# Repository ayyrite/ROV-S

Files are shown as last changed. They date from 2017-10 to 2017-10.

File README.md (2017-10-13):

# SIPI ROV-S
Documents concerning the SIPI ROV-S including electrical diagrams, stl files, and an assembly manual.

### ROV-S ROS code
ROS code for ROV-S project can be found by clicking this link -> [ROV-S Code](https://github.com/jmwest0774/rovs)

### To begin manual control of the ROV-S
* Turn on the ROV-S Intel NUC and Arduino motorshields.
* Attach a gamepad to one of the open USB ports located on the Intel NUC or USB hub connected to the Intel NUC.
* Open up a new terminal in Ubuntu.
* Type the following command below in the Ubuntu terminal that was just opened:
>
`roslaunch rovs rovs.launch`

* The ROV-S can now be controlled with the connected gamepad.

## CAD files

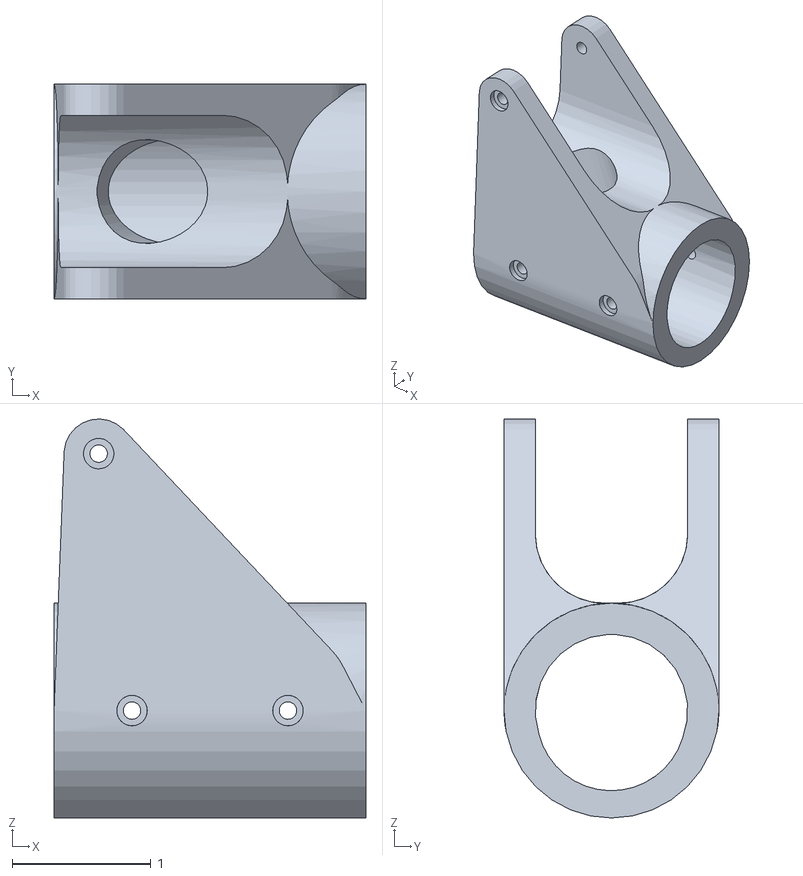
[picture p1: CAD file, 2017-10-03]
ROV-S STL/20 (x2).stl
2.25 x 1.55 x 2.88

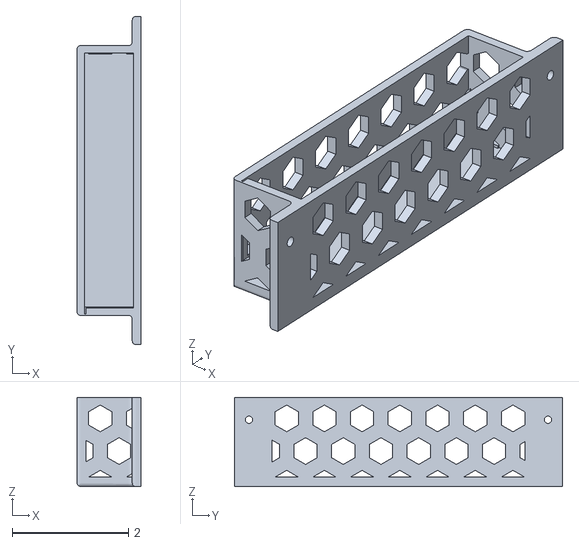
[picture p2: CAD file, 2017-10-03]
ROV-S STL/18 (x1).stl
1.10 x 5.65 x 1.53

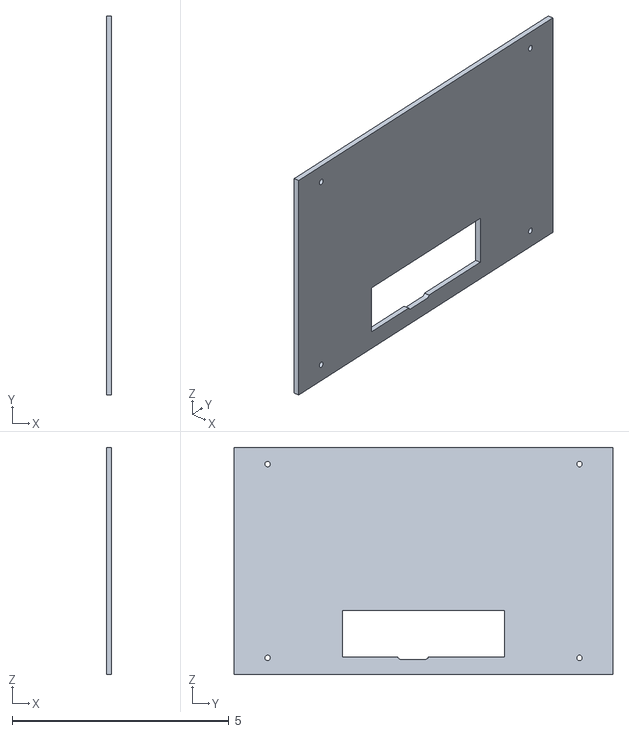
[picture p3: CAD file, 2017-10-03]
ROV-S STL/4 (x1).stl
0.125 x 8.75 x 5.25

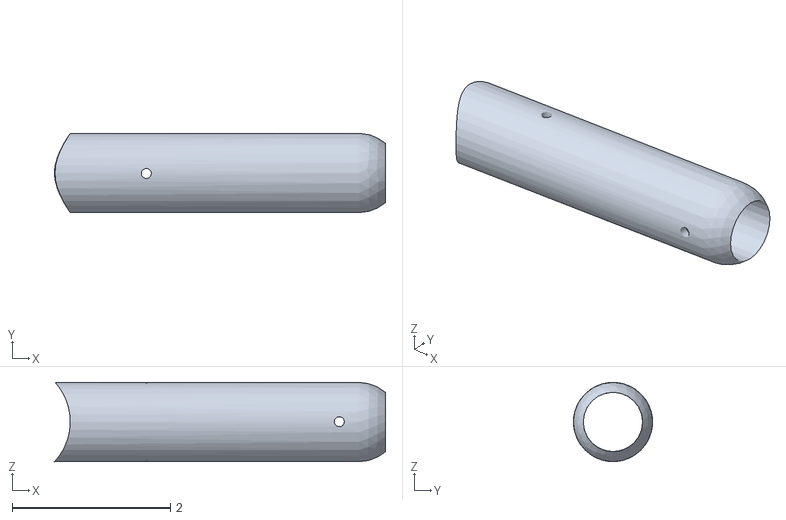
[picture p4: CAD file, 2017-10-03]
ROV-S STL/24 (x2).stl
4.18 x 1.00 x 1.00

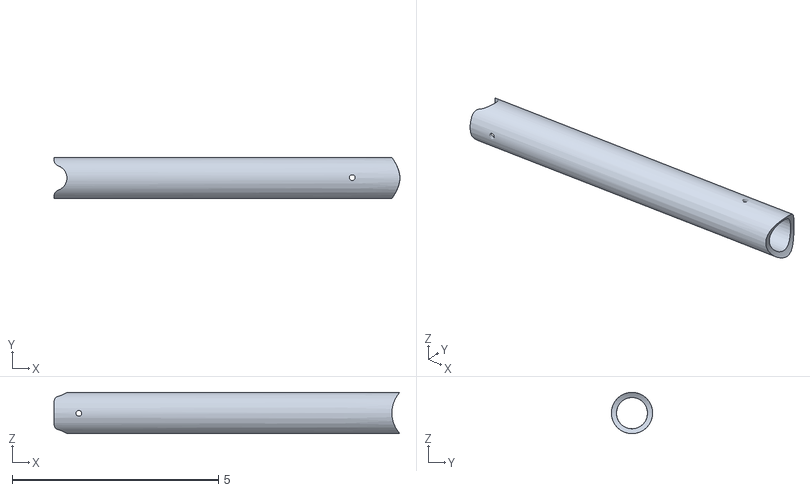
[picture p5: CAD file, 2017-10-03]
ROV-S STL/12 (x2).stl
8.38 x 1.00 x 1.00

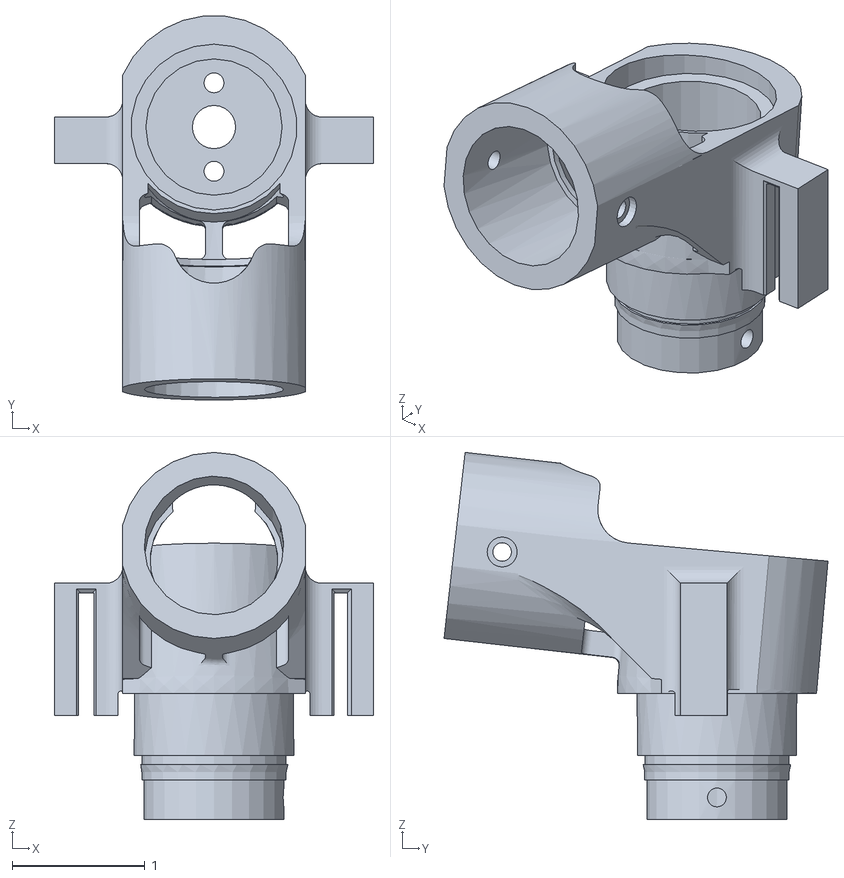
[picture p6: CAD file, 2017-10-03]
ROV-S STL/13 (x2).stl
2.40 x 2.89 x 2.77

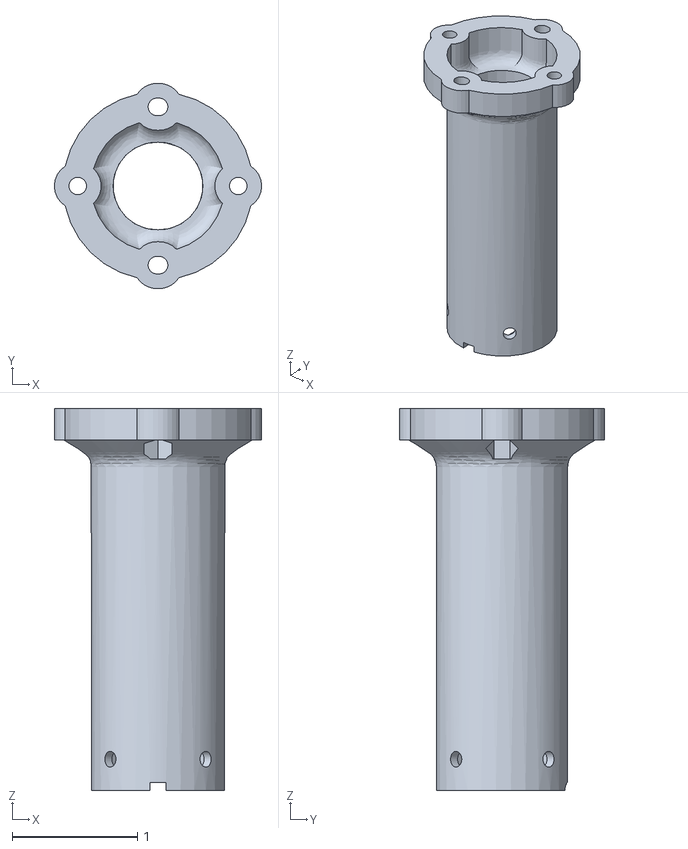
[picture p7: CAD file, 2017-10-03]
ROV-S STL/15 (x4).stl
1.66 x 1.64 x 3.05

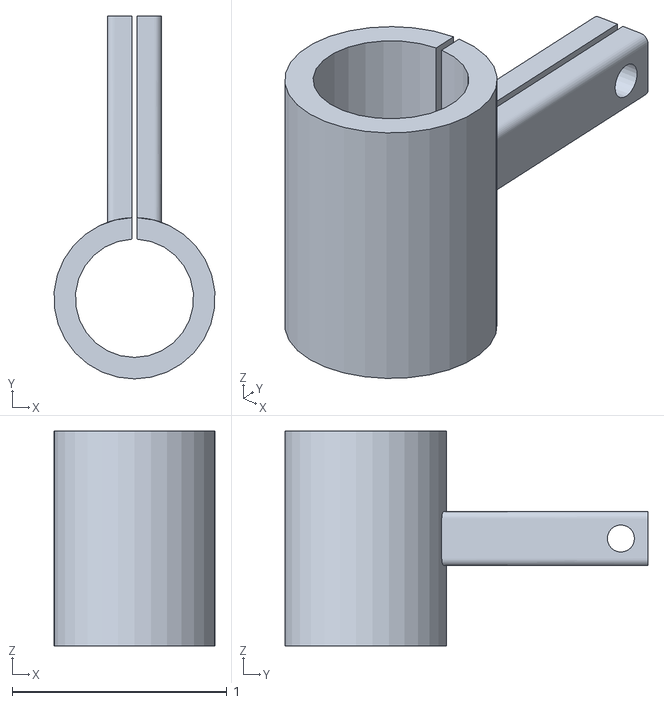
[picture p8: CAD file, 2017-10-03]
ROV-S STL/25 TPU (x1).stl
0.747 x 1.69 x 1.00

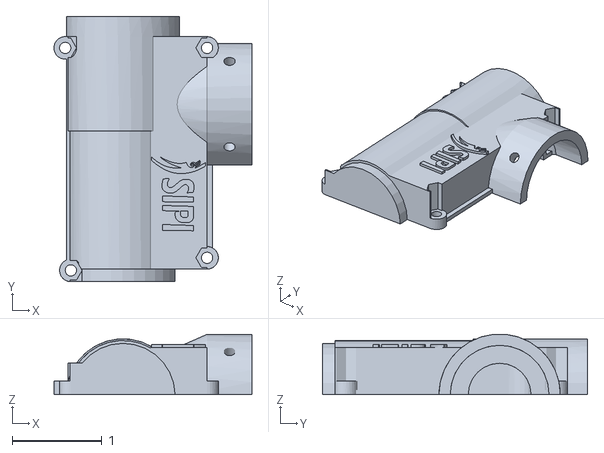
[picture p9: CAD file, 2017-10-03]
ROV-S STL/17 (x6).stl
2.20 x 2.96 x 0.672

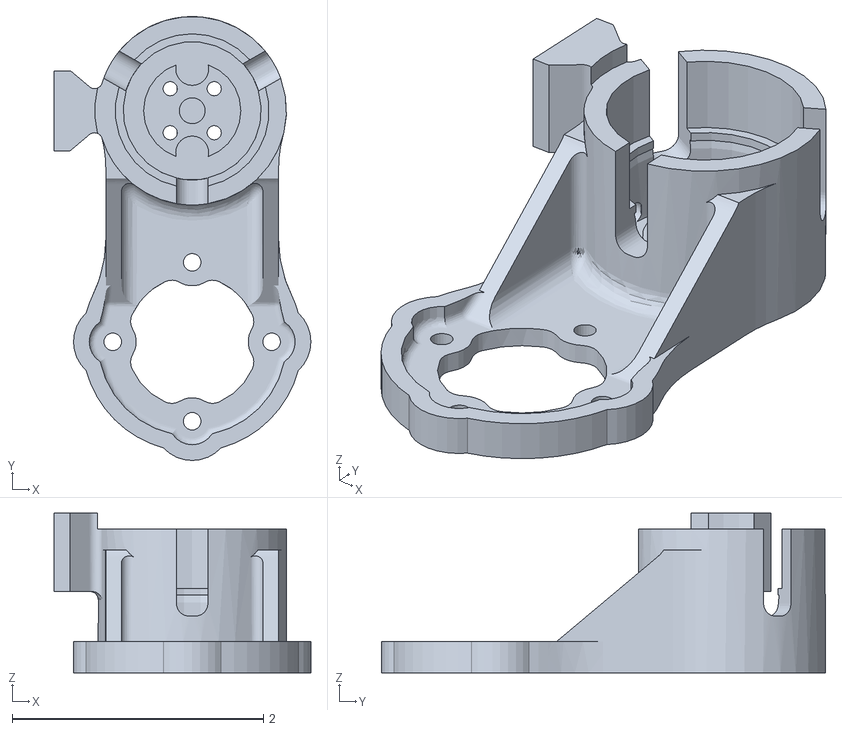
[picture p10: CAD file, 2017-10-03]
ROV-S STL/14 M (x1).stl
2.04 x 3.53 x 1.27

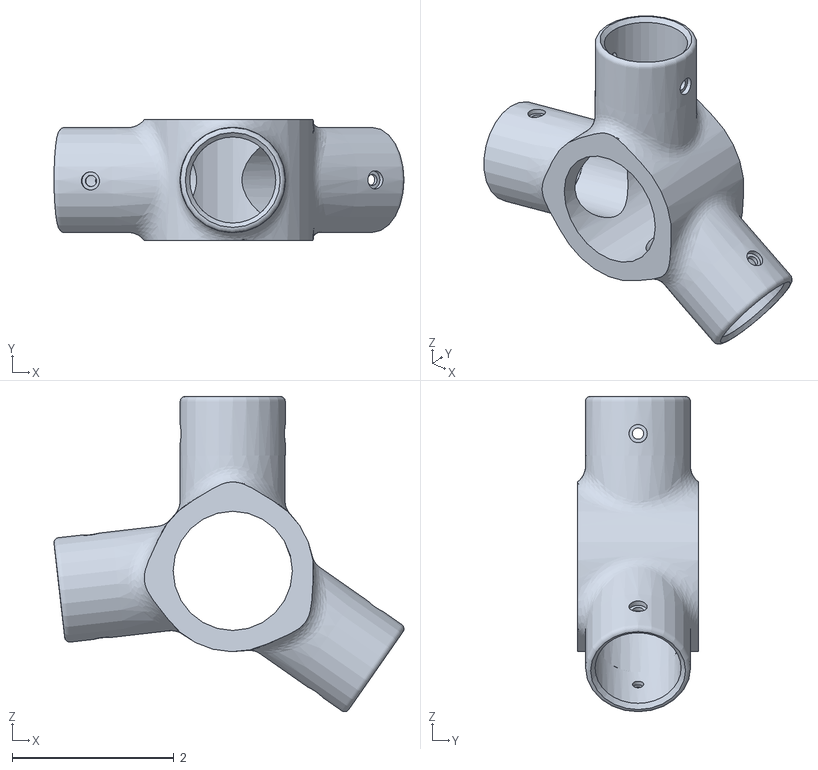
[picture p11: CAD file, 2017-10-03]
ROV-S STL/10 (x2).stl
4.33 x 1.50 x 3.90

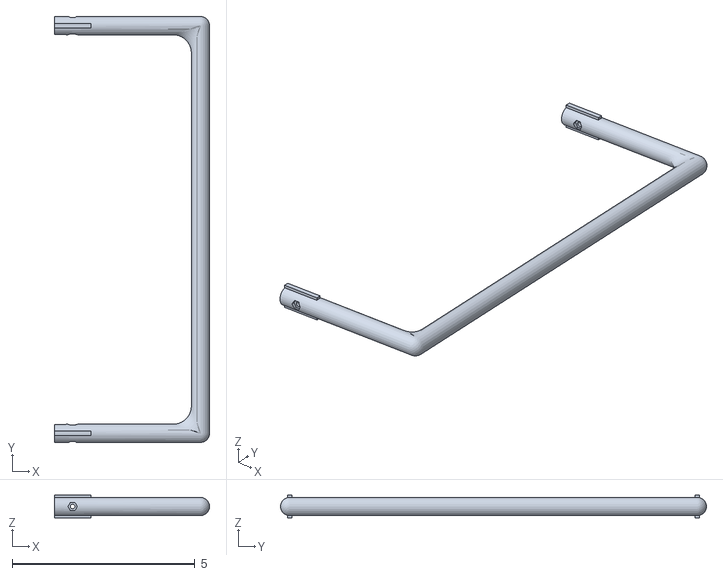
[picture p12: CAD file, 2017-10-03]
ROV-S STL/26 (x1).stl
4.25 x 11.7 x 0.626

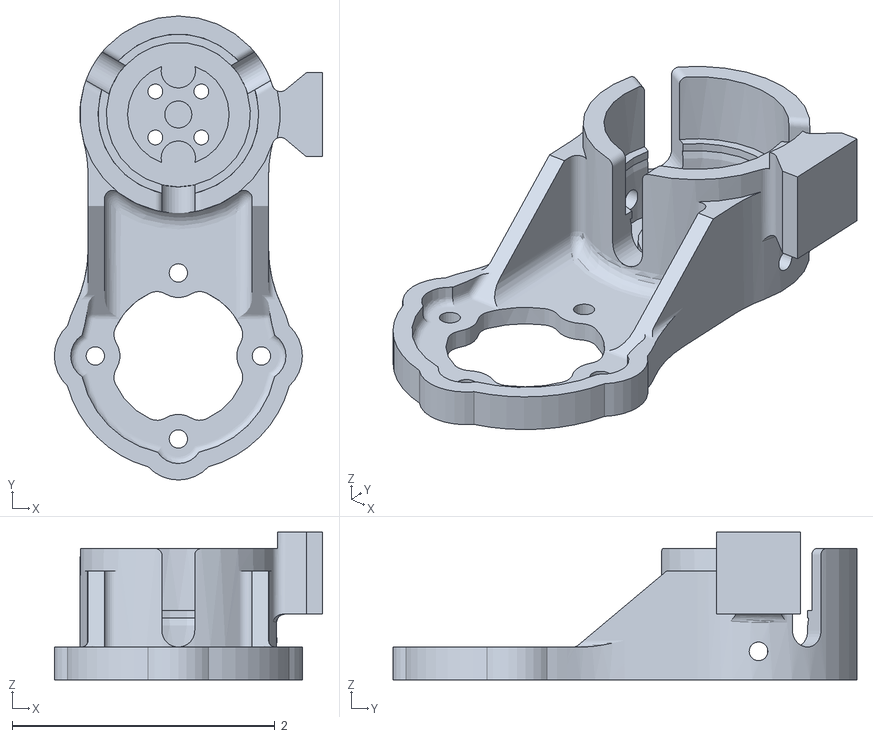
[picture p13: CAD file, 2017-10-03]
ROV-S STL/23 M (x1).stl
2.04 x 3.53 x 1.13

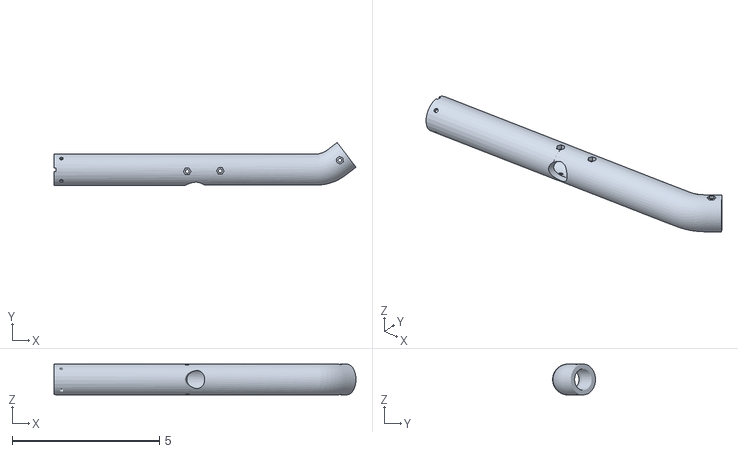
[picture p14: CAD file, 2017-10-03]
ROV-S STL/21 (x2).stl
10.3 x 1.46 x 1.05

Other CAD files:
ROV-S STL/16 (x6).stl
ROV-S STL/2 (x1).stl
ROV-S STL/7 (x8).stl
ROV-S STL/8 (x2).stl
ROV-S STL/1 (x1).stl
ROV-S STL/11 (x2).stl
ROV-S STL/14 (x1).stl
ROV-S STL/19 (x1).stl
ROV-S STL/22 (x2).stl
ROV-S STL/23 (x1).stl
ROV-S STL/27 (x4).stl
ROV-S STL/3 (x1).stl
ROV-S STL/5 (x1).stl
ROV-S STL/6 (x1).stl
ROV-S STL/9 (x2).stl

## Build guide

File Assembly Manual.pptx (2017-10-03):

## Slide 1

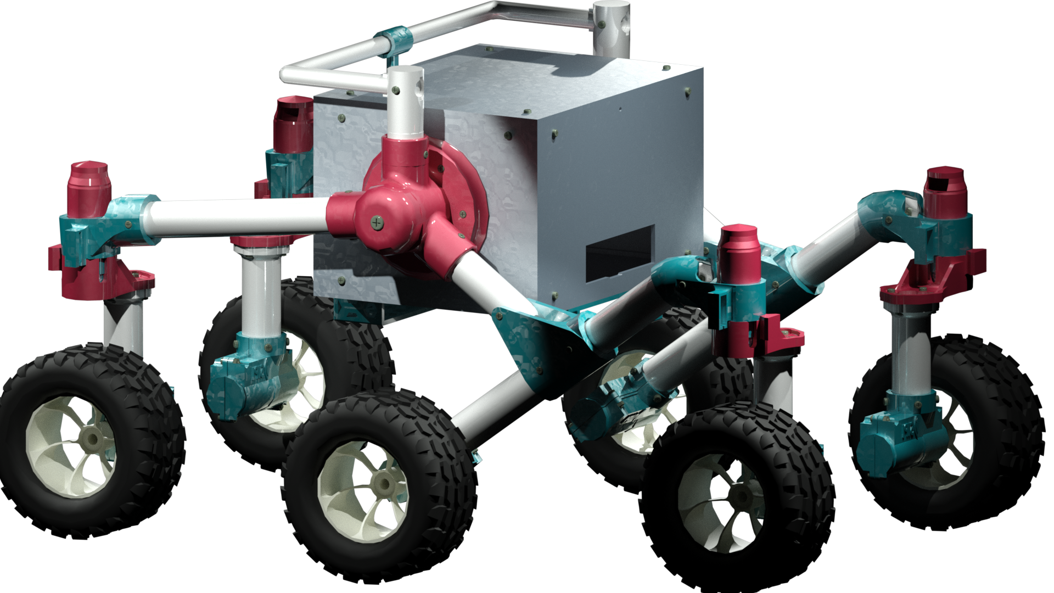
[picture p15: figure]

ROV-S ASSEMBLY MANUAL

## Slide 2

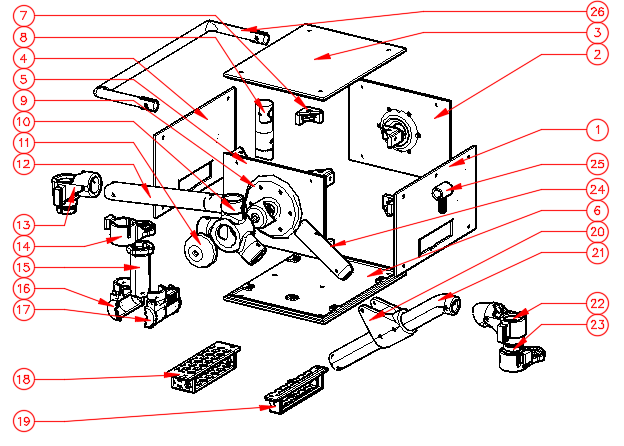
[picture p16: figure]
Screen Clipping

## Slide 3

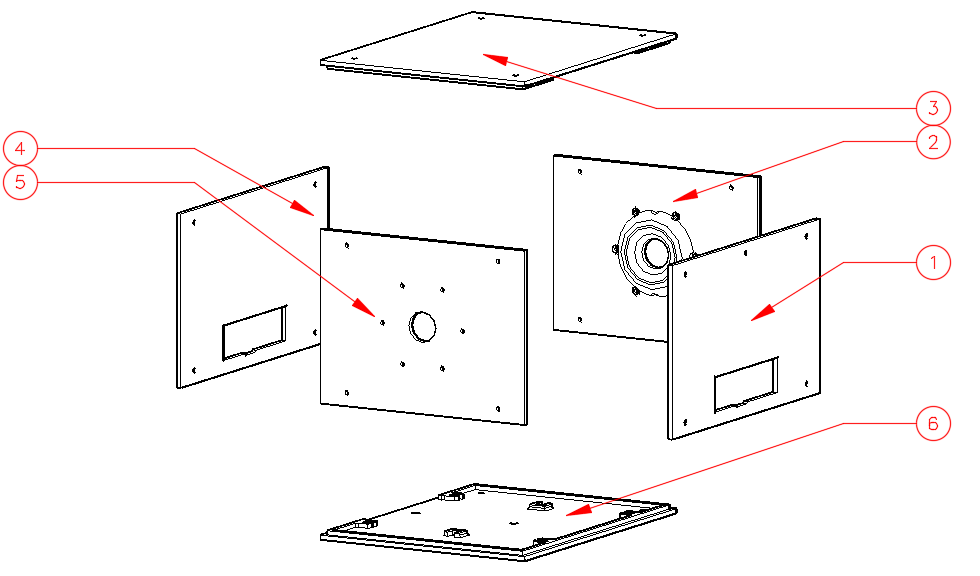
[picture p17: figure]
Screen Clipping

D1

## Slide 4

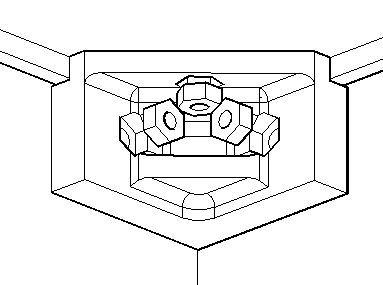
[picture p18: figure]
Screen Clipping
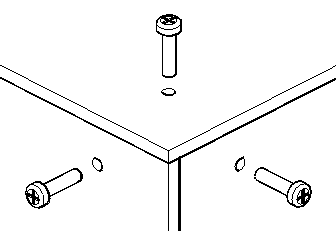
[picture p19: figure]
Screen Clipping

STEP 1

STEP 2

D1

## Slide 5

INSIDE

OUTSIDE

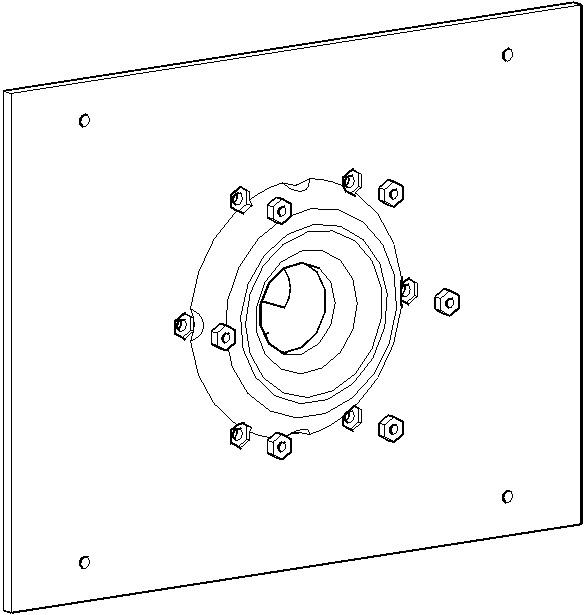
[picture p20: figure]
Screen Clipping
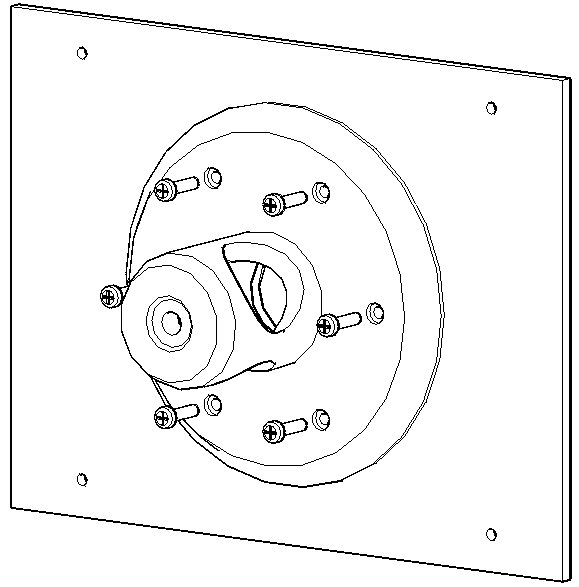
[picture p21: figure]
Screen Clipping

STEP 1

STEP 2

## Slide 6

D2

B

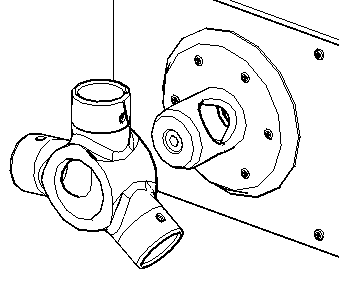
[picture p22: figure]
Screen Clipping

A

A

C

C

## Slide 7

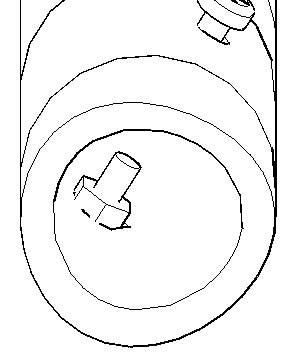
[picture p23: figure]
Screen Clipping

A

D2

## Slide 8

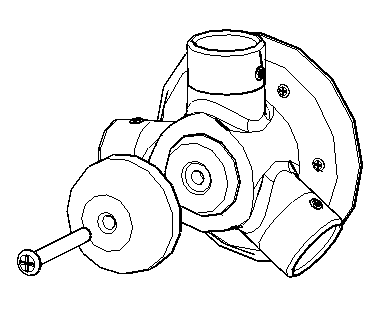
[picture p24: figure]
Screen Clipping
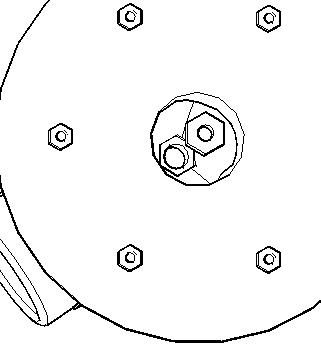
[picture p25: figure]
Screen Clipping

A

D3

A

B

C

D3

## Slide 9

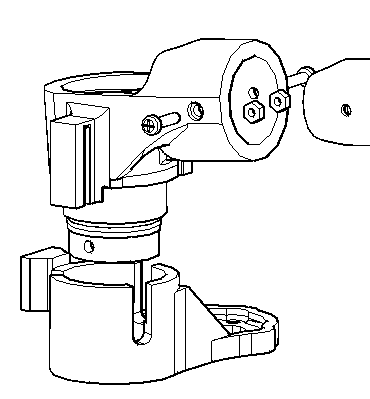
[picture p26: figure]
Screen Clipping

STEERING MOTOR INSERTED HERE

B

LIMIT SWITCH INSERTED HERE

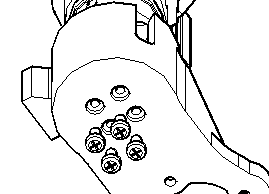
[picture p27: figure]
Screen Clipping

A

D4

C

D5

D5

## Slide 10

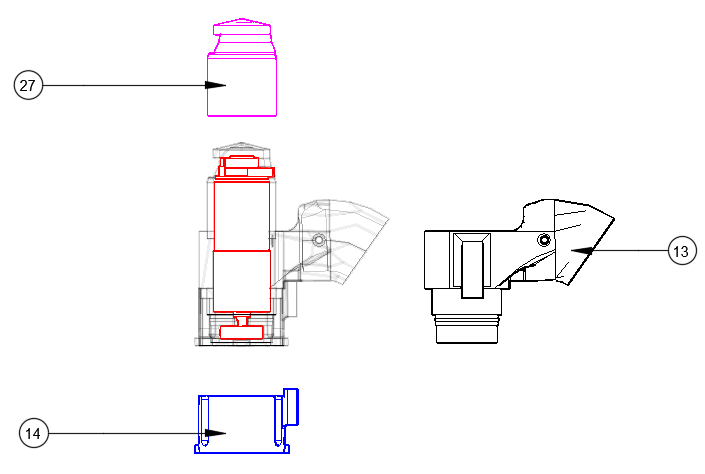
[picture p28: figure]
Screen Clipping
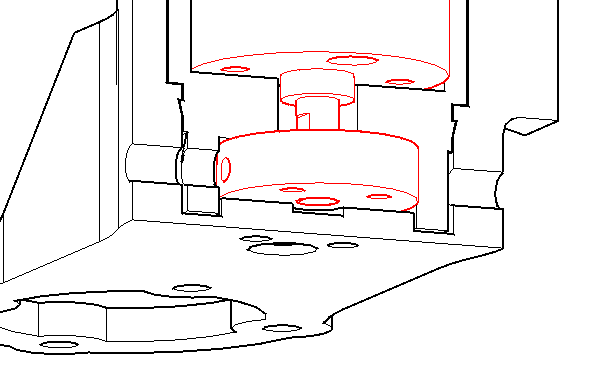
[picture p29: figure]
Screen Clipping

D4

D4

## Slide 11

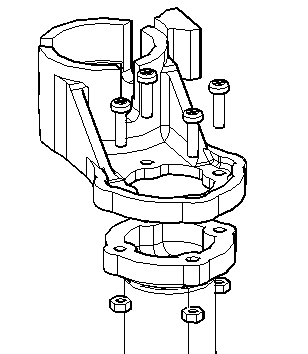
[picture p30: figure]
Screen Clipping
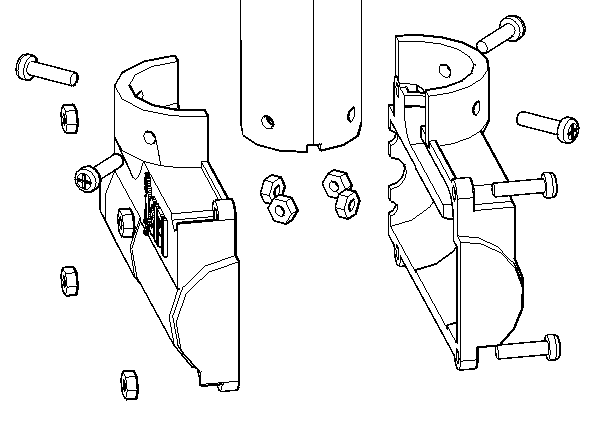
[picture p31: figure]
Screen Clipping

D

C

A

DRIVE MOTOR INSERTED HERE

B

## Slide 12

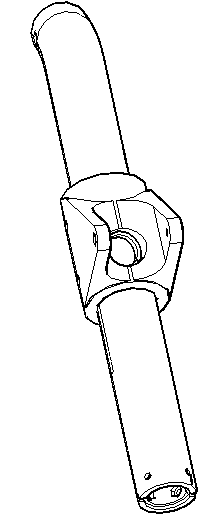
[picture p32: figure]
Screen Clipping

ALIGN HOLES FOR PROPER FIT

D6

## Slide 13

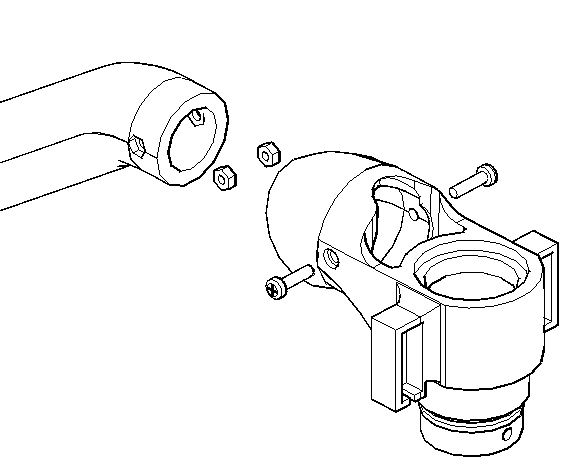
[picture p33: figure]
Screen Clipping

STEERING MOTOR INSERTED HERE

A

B

LIMIT SWITCH INSERTED HERE

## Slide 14

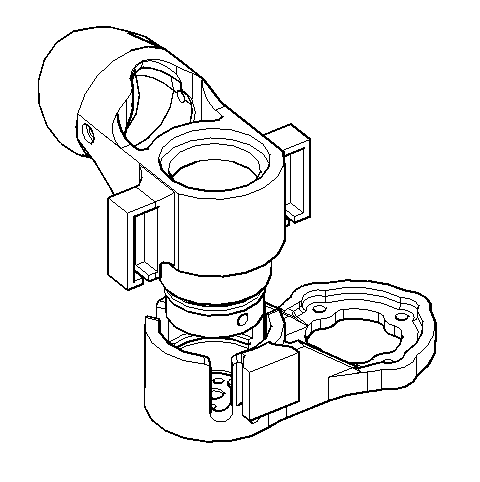
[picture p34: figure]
Screen Clipping

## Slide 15

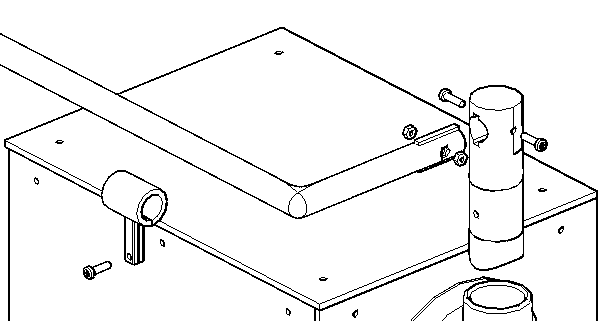
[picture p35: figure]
Screen Clipping

D

C

A

B

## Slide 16

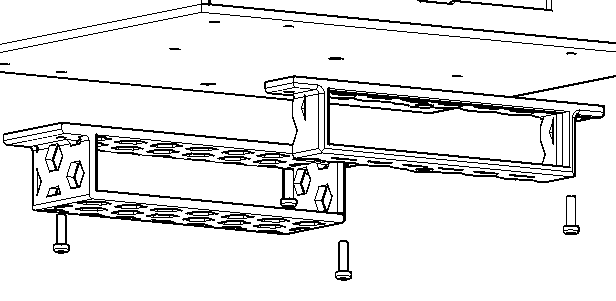
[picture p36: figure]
Screen Clipping

OUTSIDE

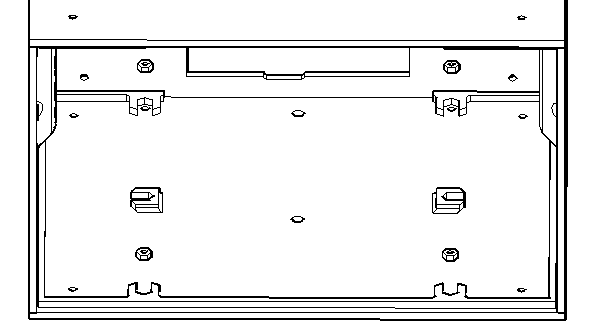
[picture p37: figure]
Screen Clipping

INSIDE

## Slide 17

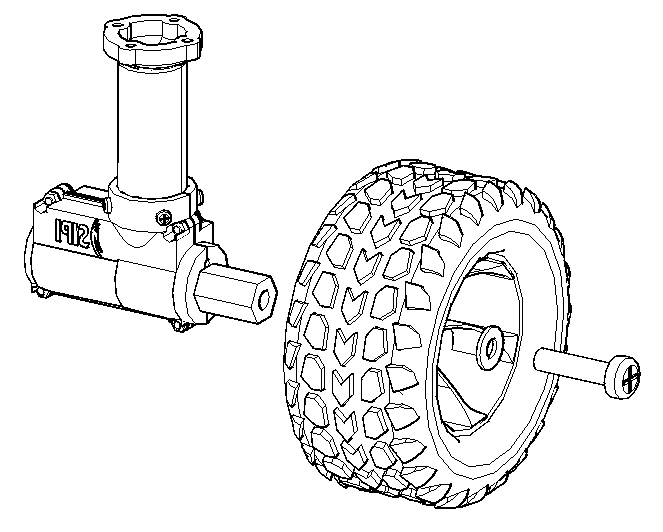
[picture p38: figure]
Screen Clipping

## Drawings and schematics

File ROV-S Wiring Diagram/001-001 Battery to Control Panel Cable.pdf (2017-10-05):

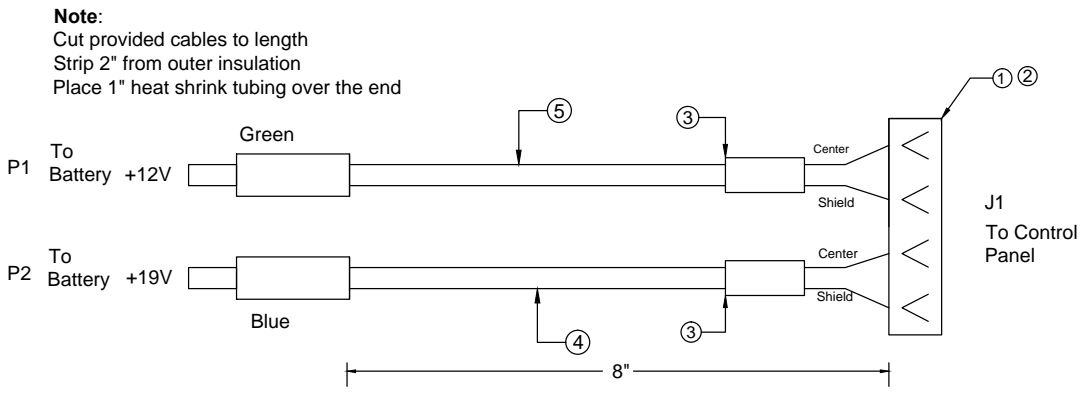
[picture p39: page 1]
Green Blue ToBattery +19V ToBattery +12V Note: Cut provided cables to length Strip 2" from outer insulation Place 1" heat shrink tubing over the end; Center Shield Center Shield; J1To Control Panel 8"; Revision; Description; Date Southwestern Indian Polytechnic Institute; Battery to Control Panel Cable Date:; DWG# 001-004 ROV - S Created: 6/16/2017; Tomczak Billie Items; Parts Number; Qty 1; Molex 4POS Recepticle; Molex Femal terminals; 3/16" Heat Shrink tubing 4; None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

Albuquerque, New Mexico

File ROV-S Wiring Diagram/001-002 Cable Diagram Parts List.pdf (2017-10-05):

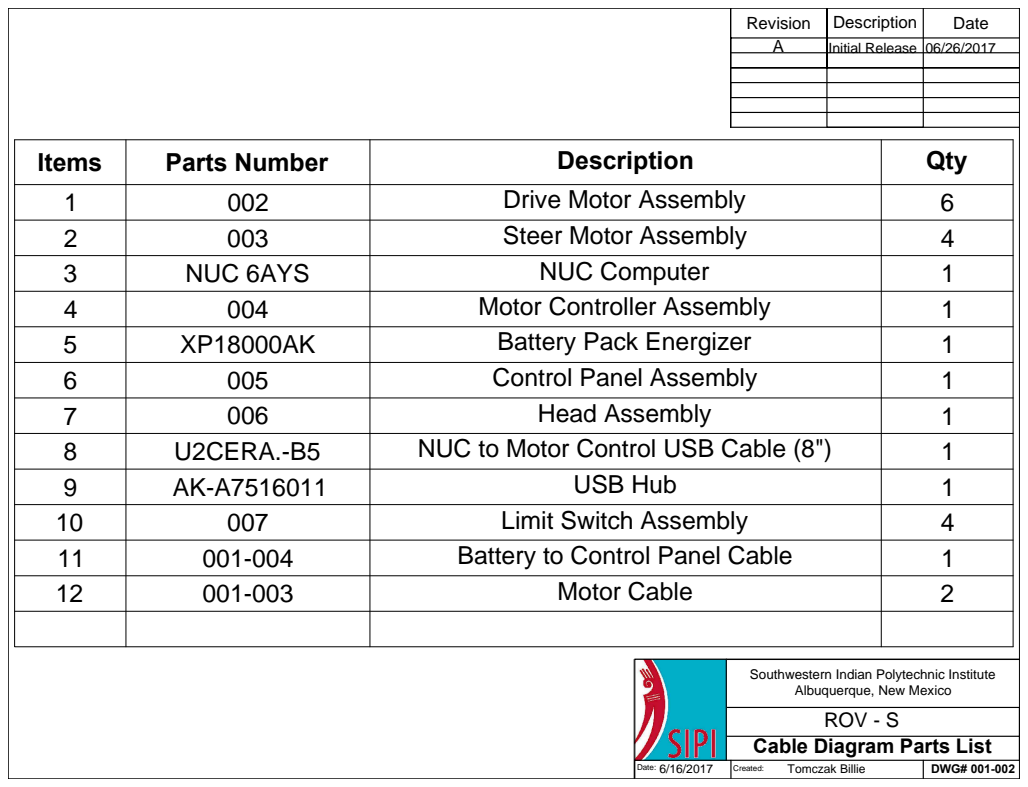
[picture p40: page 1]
Items; Parts Number; Description; Qty 1; Drive Motor Assembly; Steer Motor Assembly; NUC 6AYS; NUC Computer; Motor Controller Assembly; Battery Pack Energizer; Control Panel Assembly; Head Assembly; U2CERA.-B5; NUC to Motor Control USB Cable (8"); USB Hub; Limit Switch Assembly; Battery to Control Panel Cable; Motor Cable; 2 Revision; Date Southwestern Indian Polytechnic Institute; Cable Diagram Parts List Date:; DWG# 001-002 ROV - S Created: 6/16/2017; Tomczak Billie A; Initial Release

Albuquerque, New Mexico

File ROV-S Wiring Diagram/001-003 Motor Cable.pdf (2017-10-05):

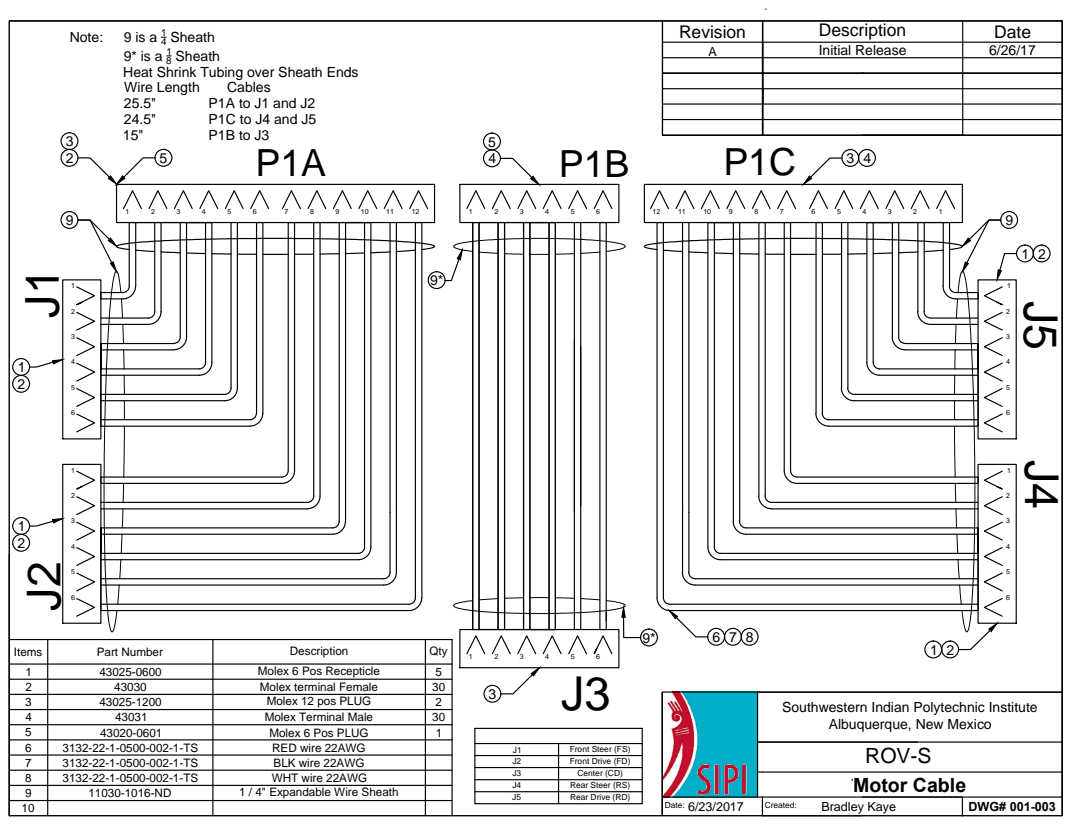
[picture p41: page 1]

J5 J4 J1 Front Steer (FS) J2 Front Drive (FD) J3 Center (CD) J4 Rear Steer (RS) J5 Rear Drive (RD) 1 2 3 4 5 6 12 11 10 9 8 7 6 5 4 3 2 1 2 5 P1A P1B P1C 39 1212 45 3 4 9 1 2 6 7 8 3 1 2 Note: 9 is a 14 Sheath 9* is a 18 Sheath Heat Shrink Tubing over Sheath Ends Wire Length Cables 25.5" P1A to J1 and J2 24.5" P1C to J4 and J5 15" P1B to J3 9* 9* Southwestern Indian Polytechnic Institute Albuquerque, New Mexico Motor Cable Date: DWG# 001-003 ROV-S Created: Description Date 6/23/2017 Bradley Kaye Initial Release Revision A 6/26/17

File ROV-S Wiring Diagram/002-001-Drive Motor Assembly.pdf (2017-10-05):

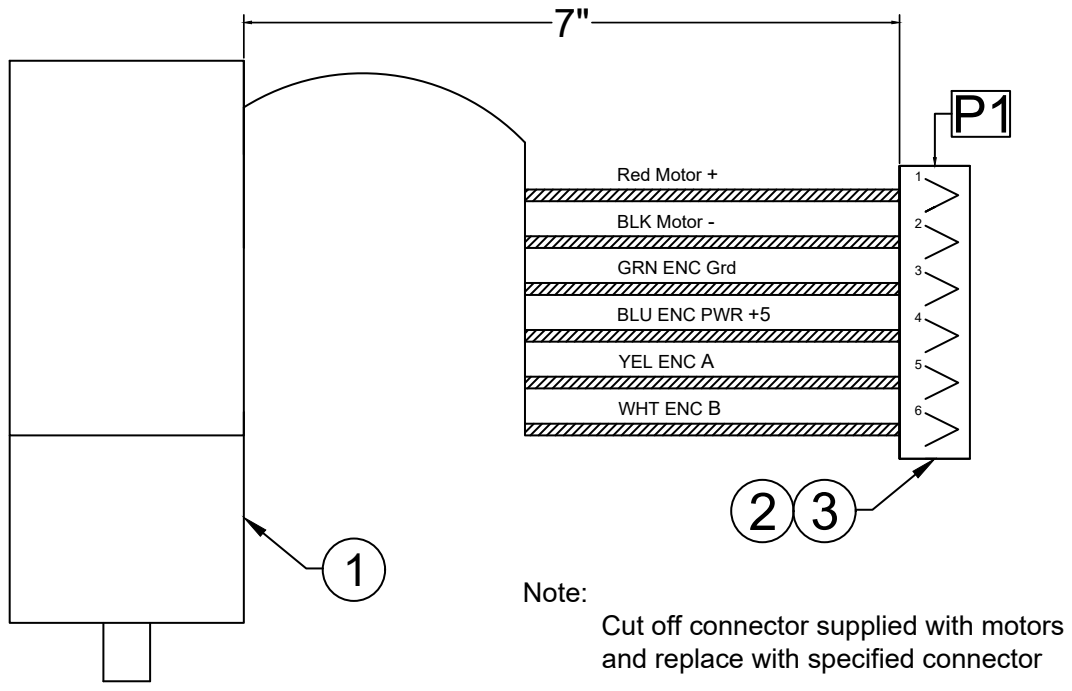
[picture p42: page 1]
Note: Cut off connector supplied with motors; and replace with specified connector Red Motor + BLK Motor - GRN ENC Grd BLU ENC PWR +5 YEL ENC A WHT ENC B 7"; Revision; Description; Date Southwestern Indian Polytechnic Institute; Drive Motor Assembly Date:; DWG# 002-001 ROV - S Created: 6/16/2017; Tomczak Billie Items; Parts Number; Qty 1; Pololu Gear Motor 31 rpm; Molex 6 Pos Plug; Molex Pins (Male); Initial Release

Albuquerque, New Mexico

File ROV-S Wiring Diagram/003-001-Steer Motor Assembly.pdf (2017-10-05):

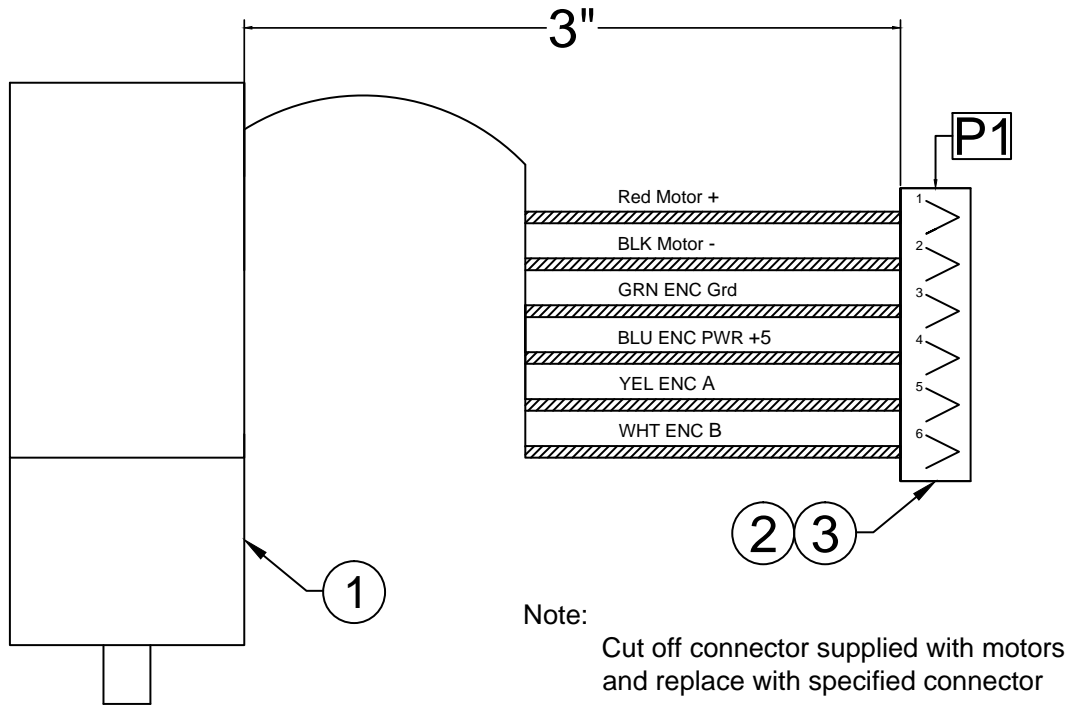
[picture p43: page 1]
Note: Cut off connector supplied with motors; and replace with specified connector Red Motor + BLK Motor - GRN ENC Grd BLU ENC PWR +5 YEL ENC A WHT ENC B 3"; Revision; Description; Date Southwestern Indian Polytechnic Institute; Steer Motor Assembly Date:; DWG# 003-001 ROV - S Created: 6/16/2017; Tomczak Billie Items; Parts Number; Qty 1; Pololu Gear Motor 16 rpm; molex 6 Pos Plug; Molex Pins (Male); Initial Release

Albuquerque, New Mexico

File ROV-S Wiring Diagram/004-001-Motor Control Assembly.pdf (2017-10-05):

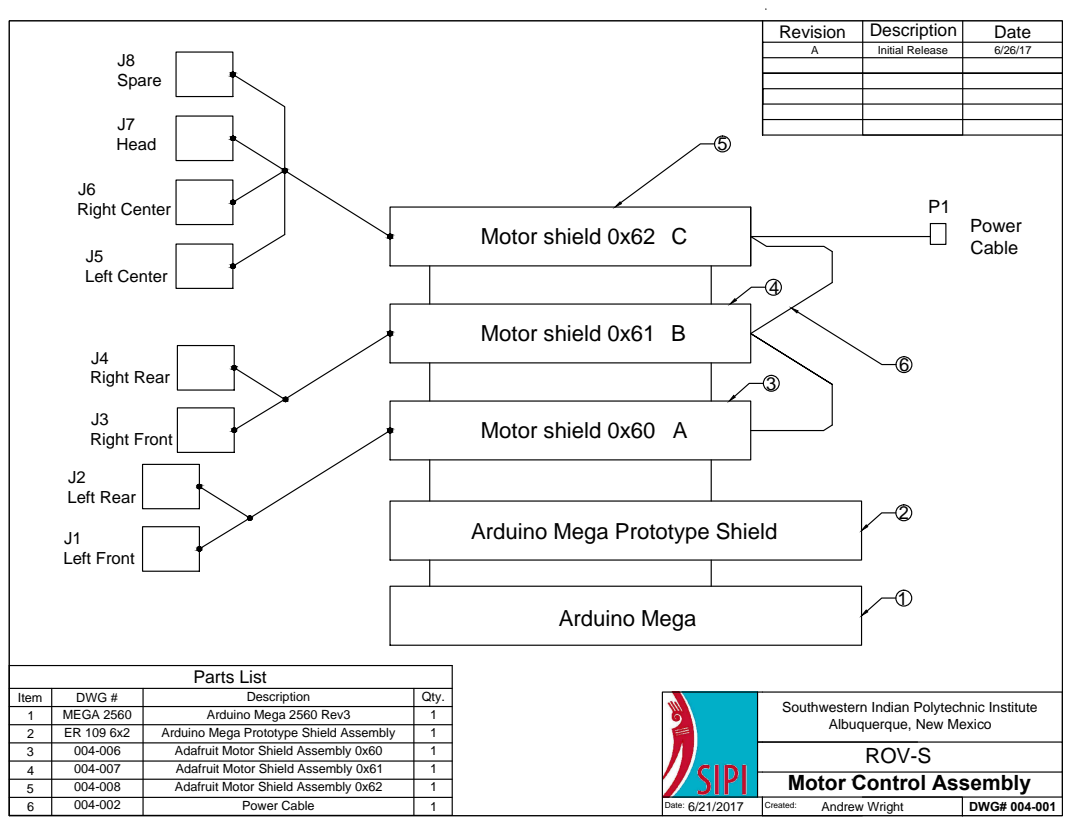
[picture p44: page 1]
J8Spare J7Head J6Right Center J5Left Center J4Right Rear J3Right Front J2Left Rear J1Left Front; Motor shield 0x62 C Motor shield 0x61 B Motor shield 0x60 A Arduino Mega Prototype Shield; Arduino Mega 5; Power Cable 21 Southwestern Indian Polytechnic Institute; Motor Control Assembly Date:; DWG# 004-001 ROV-S Created: Revision; Description; Date 6/21/2017; Andrew Wright A; Initial Release; 6/26/17 Parts List Item; DWG #; Qty. 1; MEGA 2560; Arduino Mega 2560 Rev3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

Albuquerque, New Mexico

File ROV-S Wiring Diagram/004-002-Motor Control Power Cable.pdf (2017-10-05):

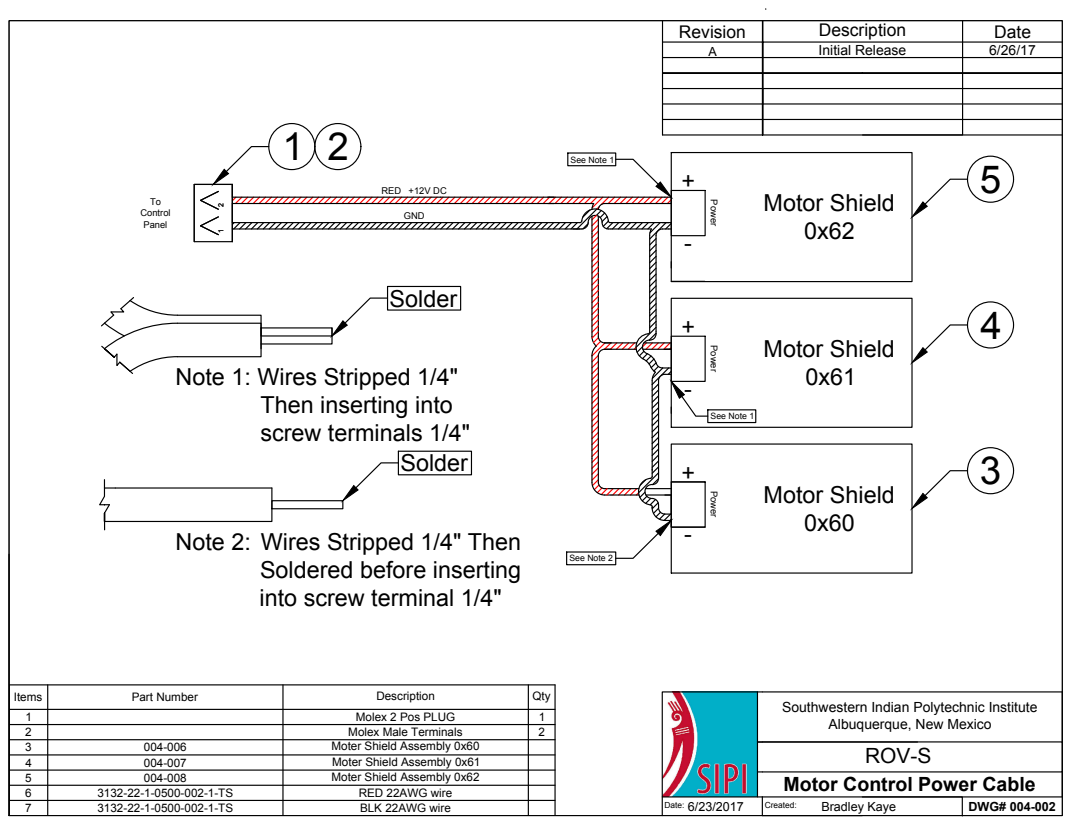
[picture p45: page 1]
Power +-

Power Motor Shield 0x62 Motor Shield 0x61 Motor Shield 0x60 543 1 See Note 1 See Note 1 See Note 2 To Control Panel Solder Note 1: Wires Stripped 1/4" Then inserting into screw terminals 1/4" Note 2: Wires Stripped 1/4" Then Soldered before inserting into screw terminal 1/4" GND RED +12V DC 2 Solder Items Part Number Description Qty 1 Molex 2 Pos PLUG 1 2 Molex Male Terminals 2 3 004-006 Moter Shield Assembly 0x60 4 004-007 Moter Shield Assembly 0x61 5 004-008 Moter Shield Assembly 0x62 6 3132-22-1-0500-002-1-TS RED 22AWG wire 7 3132-22-1-0500-002-1-TS BLK 22AWG wire Southwestern Indian Polytechnic Institute Albuquerque, New Mexico Motor Control Power Cable Date: DWG# 004-002 ROV-S Created: Description Date 6/23/2017 Bradley Kaye Initial Release Revision A 6/26/17

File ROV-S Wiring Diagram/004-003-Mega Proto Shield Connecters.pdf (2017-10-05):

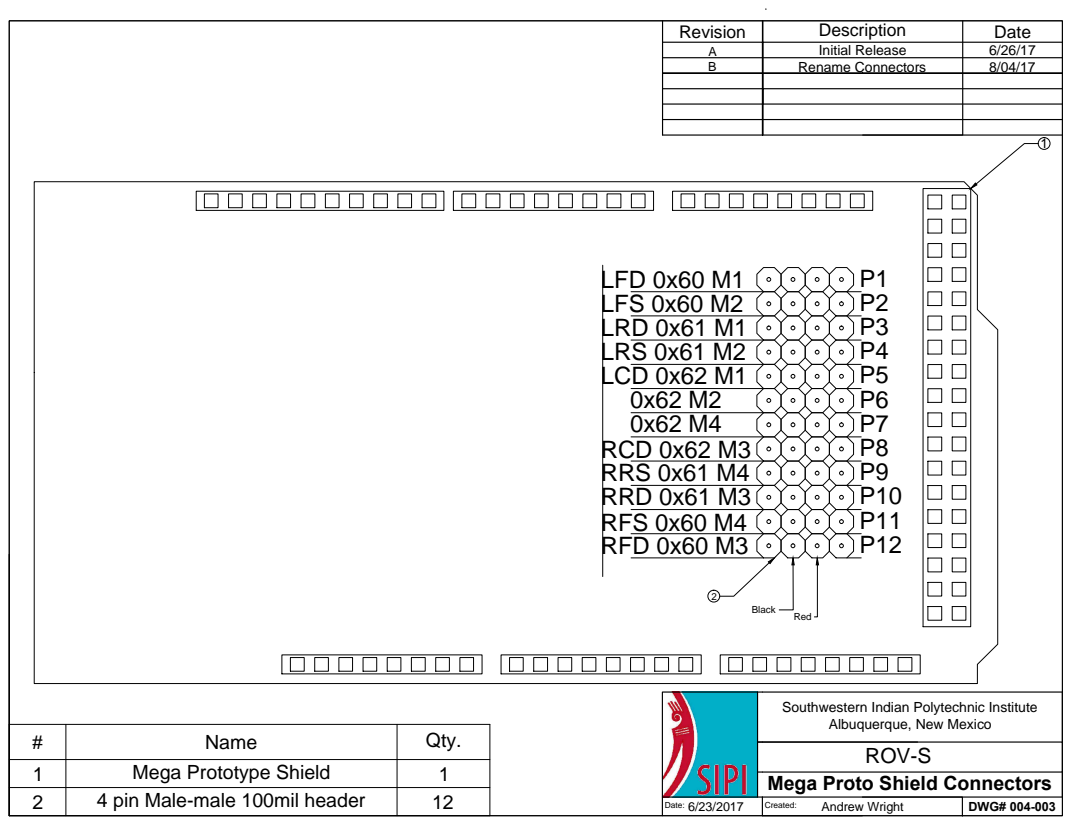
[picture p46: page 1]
LFD 0x60 M1 LFS 0x60 M2 LRD 0x61 M1 LRS 0x61 M2 LCD 0x62 M1 0x62 M2 0x62 M4 RCD 0x62 M3 RRS 0x61 M4 RRD 0x61 M3 RFS 0x60 M4 RFD 0x60 M3; Black; Red Southwestern Indian Polytechnic Institute; Mega Proto Shield Connectors Date:; DWG# 004-003 ROV-S Created:; Description; Date 6/23/2017; Andrew Wright Initial Release Revision A; Name; Qty. 1; Mega Prototype Shield; 4 pin Male-male 100mil header; Rename Connectors

Albuquerque, New Mexico

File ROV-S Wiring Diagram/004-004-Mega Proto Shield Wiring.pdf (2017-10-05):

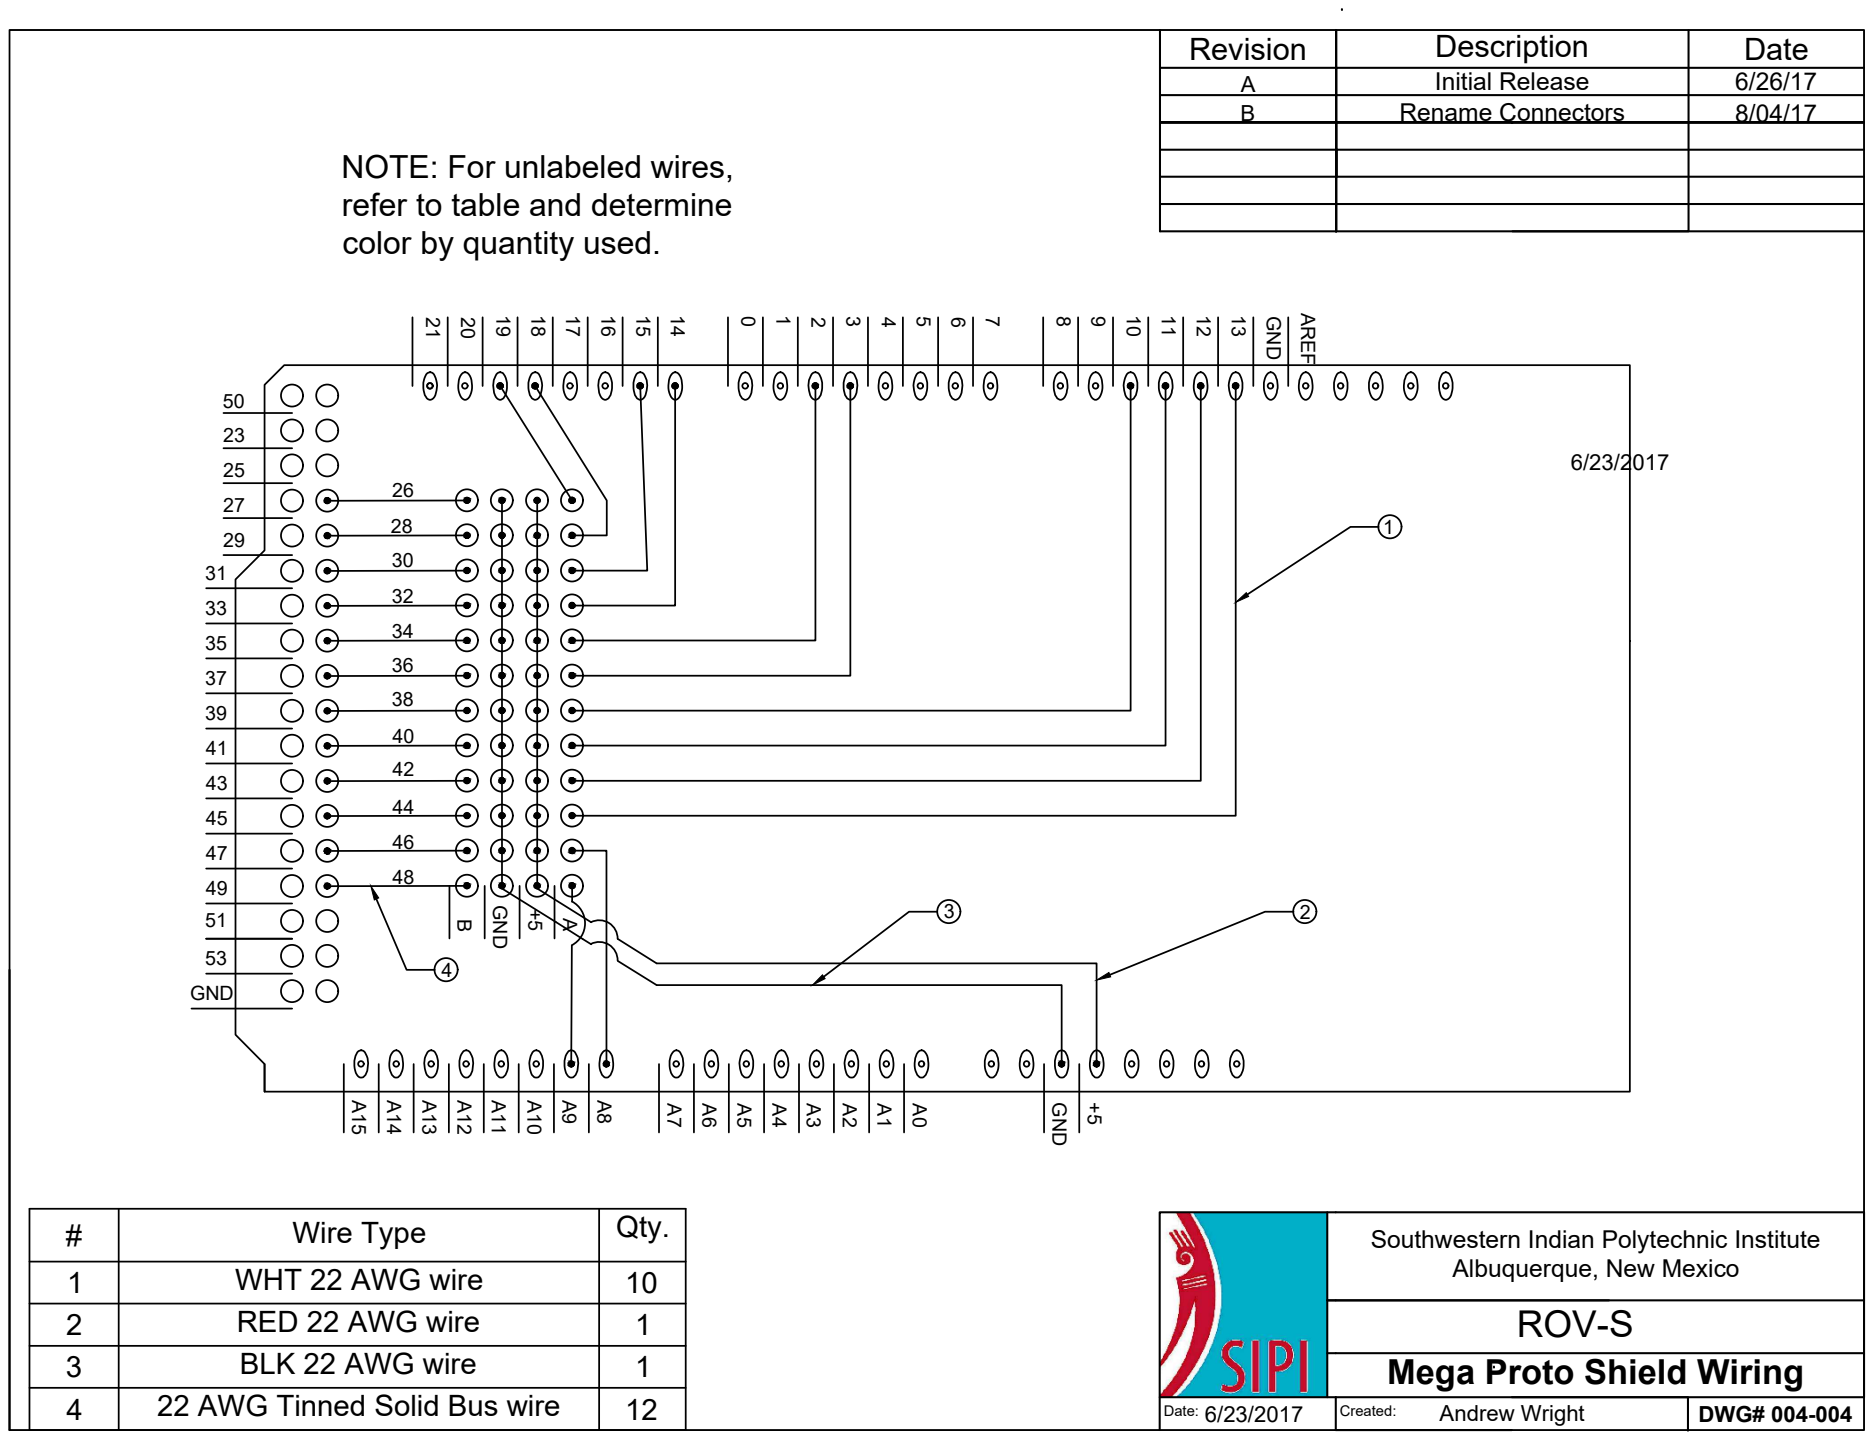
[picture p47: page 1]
AREF 5023252729 313335373941434547495153 GND; Mega Proto Shield Wiring Date:; DWG# 004-004 ROV-S Created:; Description; Date 6/23/2017; Andrew Wright Initial Release Revision A; Wire Type; Qty. 1; WHT 22 AWG wire; RED 22 AWG wire; BLK 22 AWG wire; 22 AWG Tinned Solid Bus wire; Rename Connectors

+5B 1 3 2 4 NOTE: For unlabeled wires, refer to table and determine color by quantity used. 262830323436384042444648 Southwestern Indian Polytechnic Institute

Albuquerque, New Mexico

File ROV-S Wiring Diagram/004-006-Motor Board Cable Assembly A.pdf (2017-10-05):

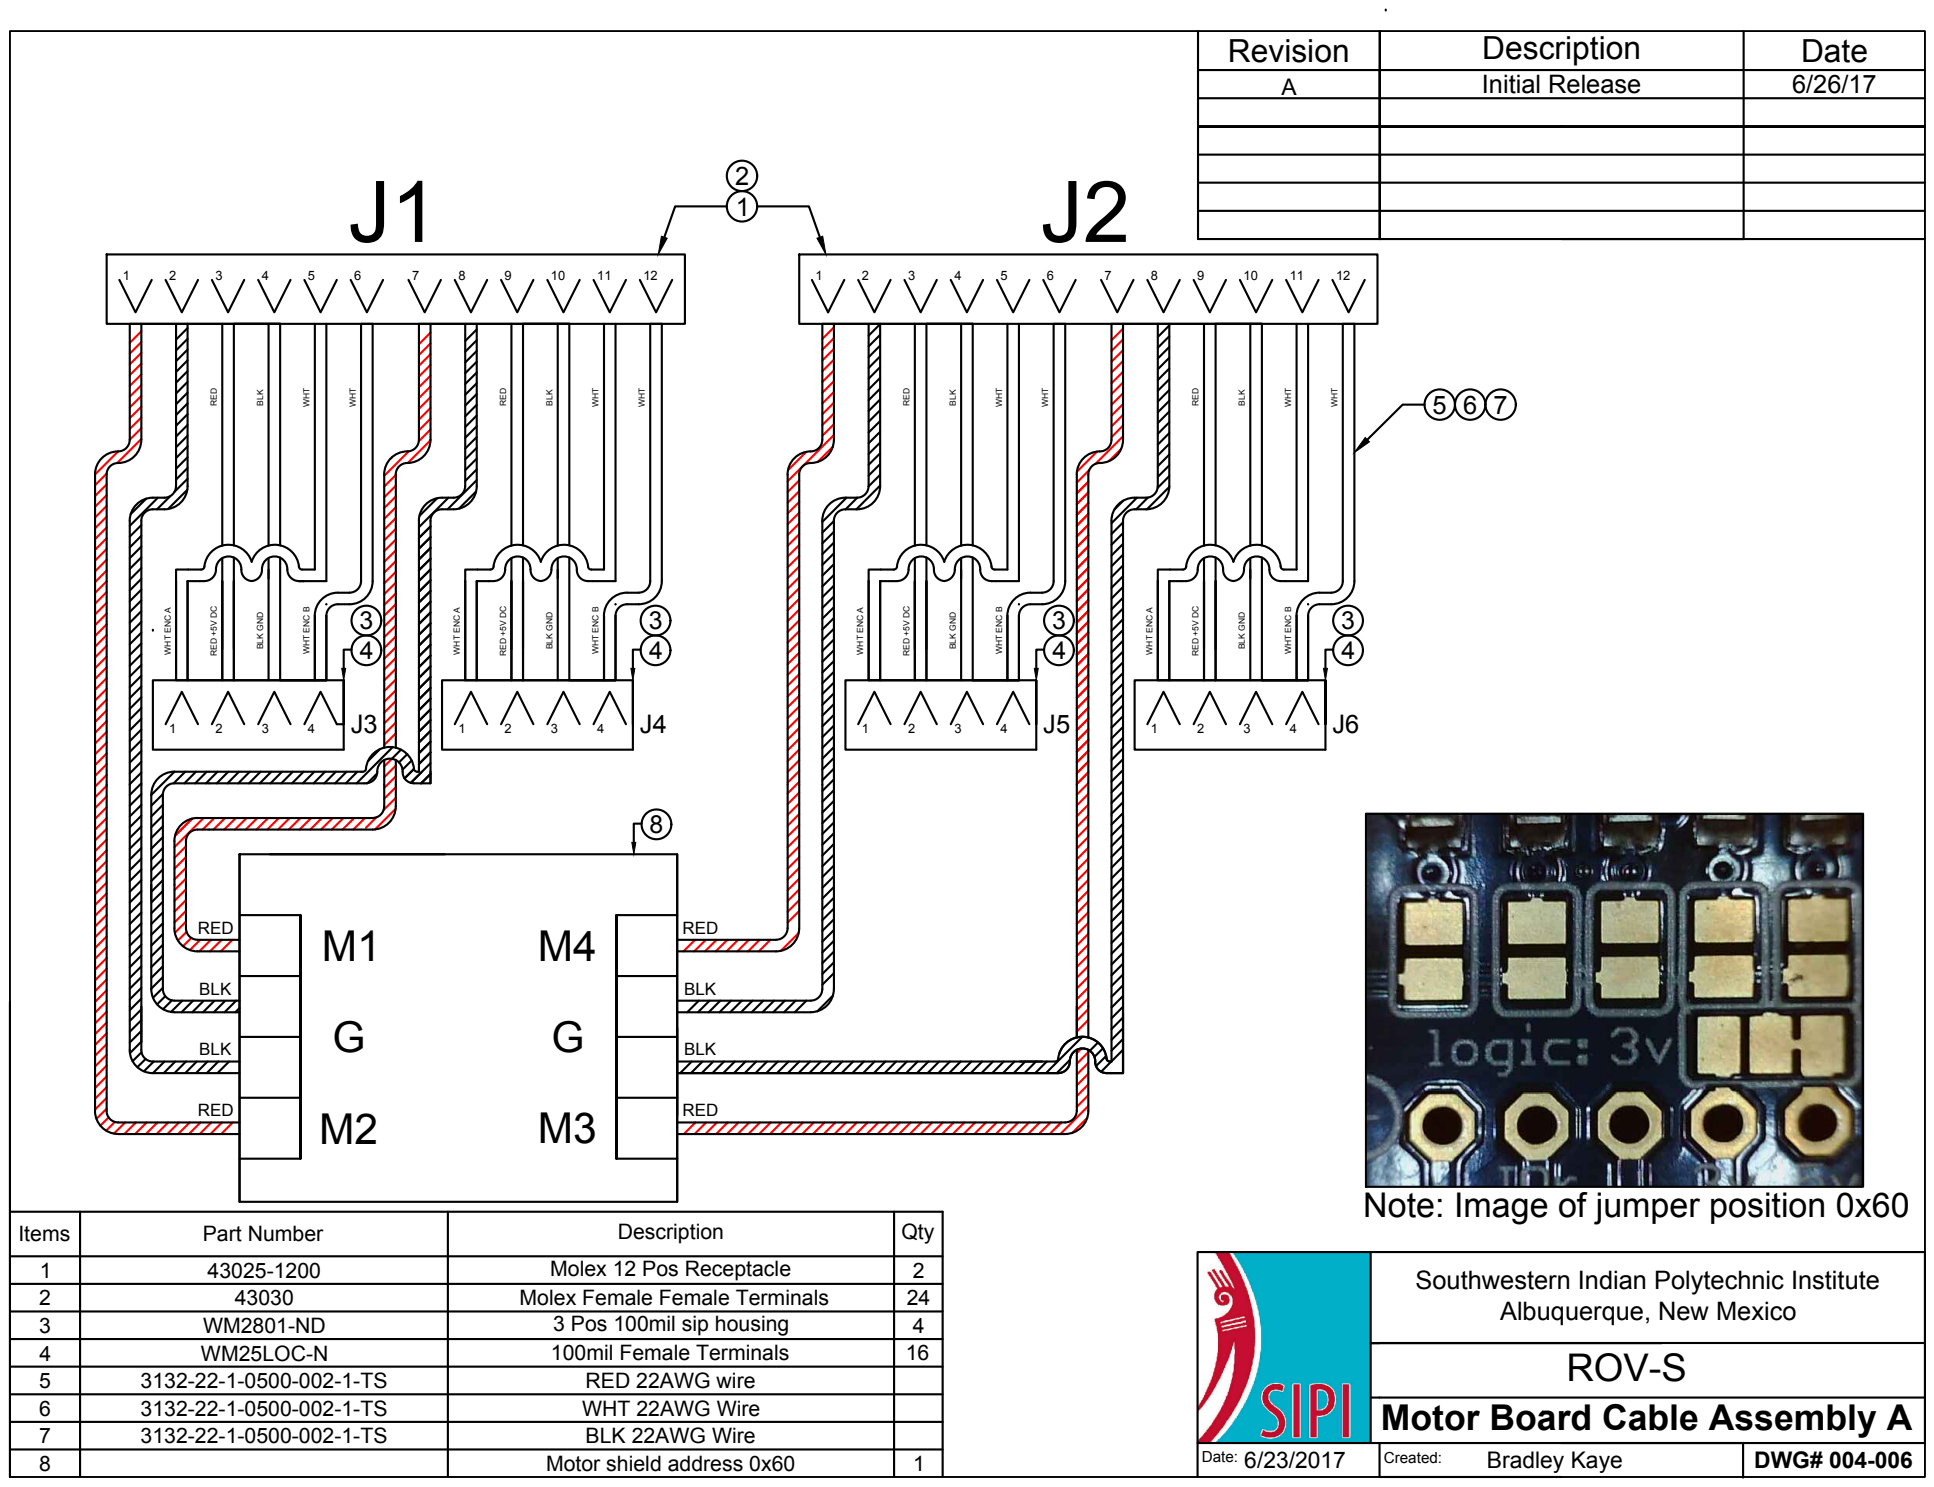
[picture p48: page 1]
BLK BLK 4 G BLK RED; WHT ENC A; BLK GND

BLK WHT WHT Items Part Number Description Qty 1 43025-1200 Molex 12 Pos Receptacle 2 2 43030 Molex Female Female Terminals 24 3 WM2801-ND 3 Pos 100mil sip housing 4 4 WM25LOC-N 100mil Female Terminals 16 5 3132-22-1-0500-002-1-TS RED 22AWG wire 6 3132-22-1-0500-002-1-TS WHT 22AWG Wire 7 3132-22-1-0500-002-1-TS BLK 22AWG Wire 8 Motor shield address 0x60 1 12 5 6 7 ..\..\..\Desktop\ROV- S\0x60.jpg Note: Image of jumper position 0x60 8 Southwestern Indian Polytechnic Institute Albuquerque, New Mexico Motor Board Cable Assembly A Date: DWG# 004-006 ROV-S Created: Description Date 6/23/2017 Bradley Kaye Initial Release Revision A 6/26/17

BLK GND WHT WHT ENC B J1 J2 1 2 3 4 5 6 7 8 9 10 11 12 J3 J6 3 3 4 M2 M4 M3 BLK RED RED

BLK WHT ENC A RED

WHT WHT RED +5V DC RED

RED +5V DC WHT WHT ENC B WHT WHT ENC A

BLK BLK GND

RED +5V DC WHT ENC B RED

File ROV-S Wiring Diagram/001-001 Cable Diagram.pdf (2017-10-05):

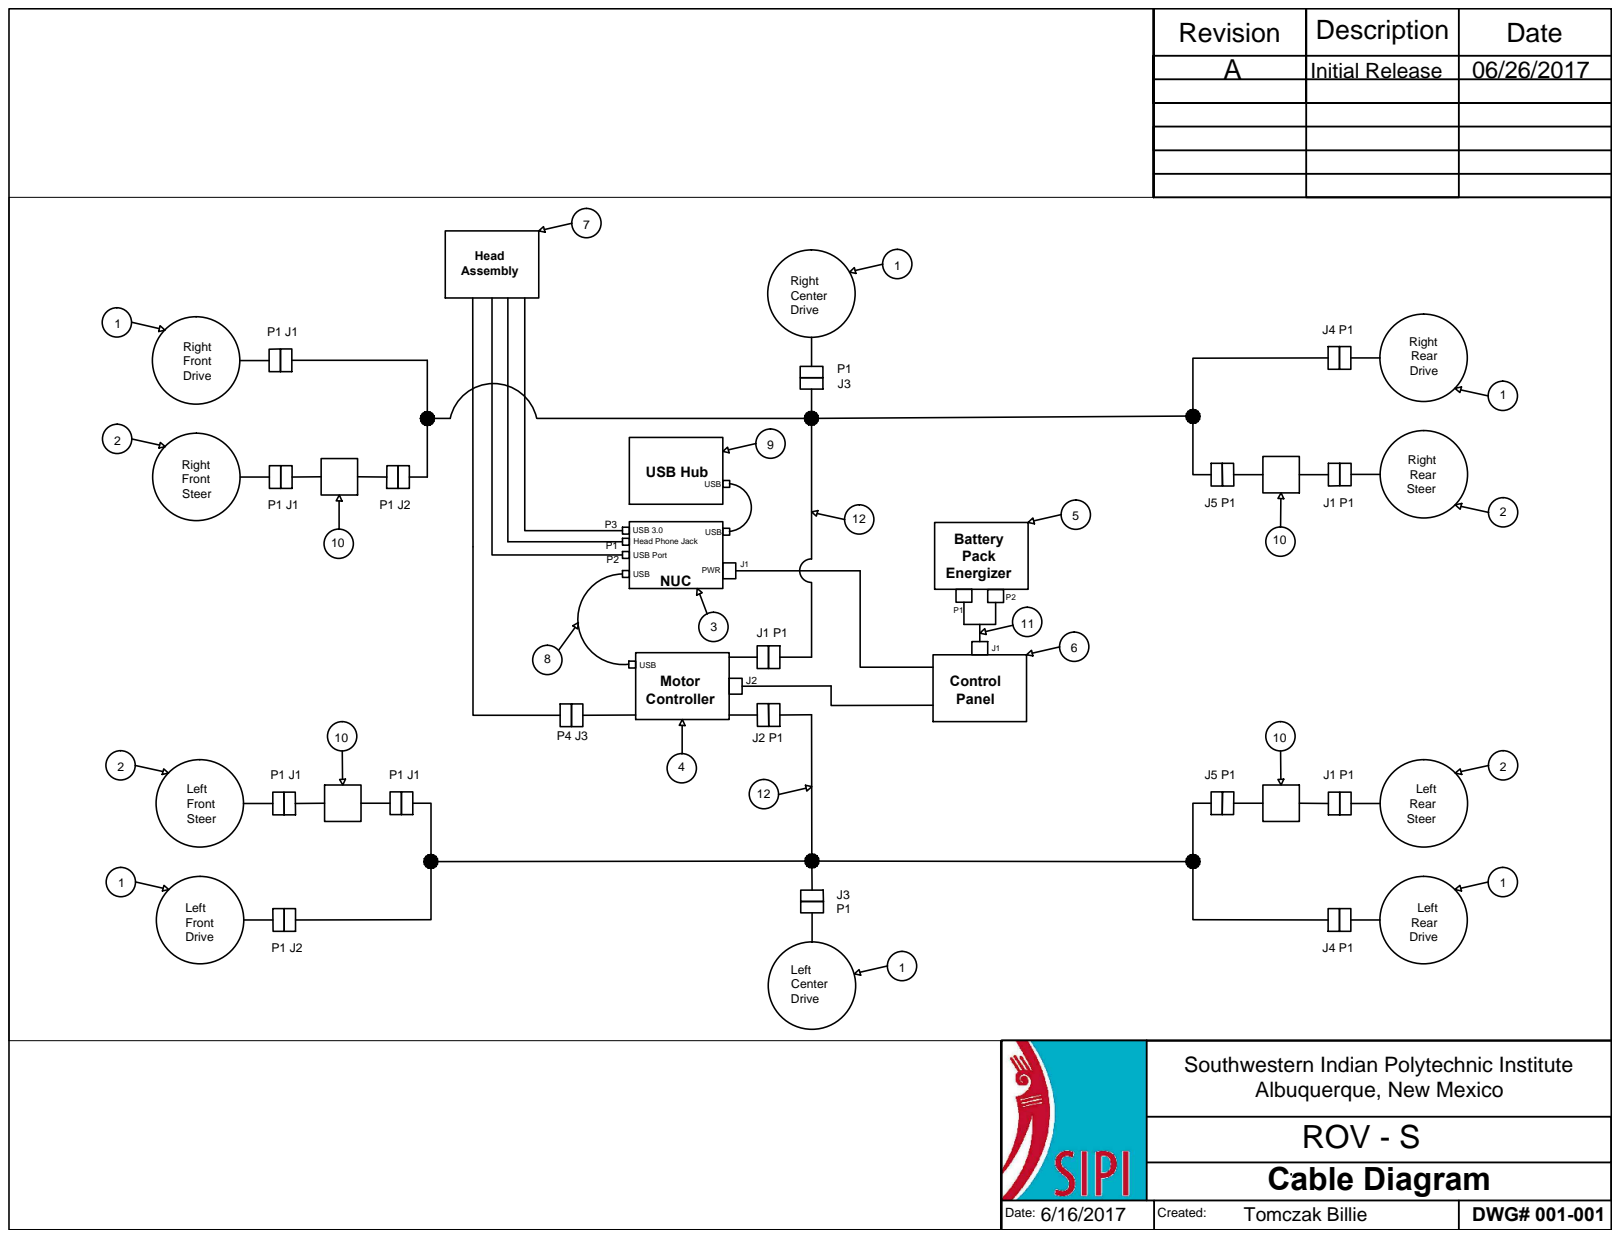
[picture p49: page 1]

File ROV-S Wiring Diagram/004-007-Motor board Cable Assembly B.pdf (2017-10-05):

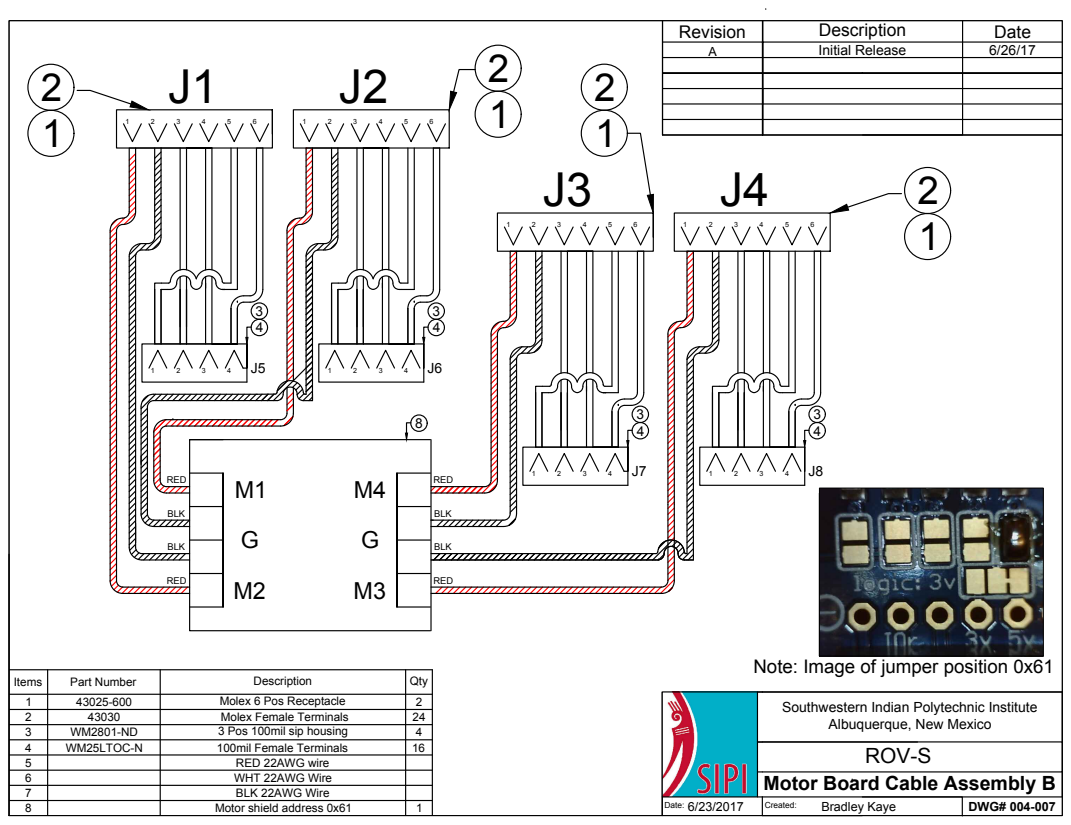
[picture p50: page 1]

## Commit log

2017-10-03 STL files
    files used to 3d print the ROV-S
    [1 (x1).stl, 10 (x2).stl, 11 (x2).stl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]
2017-10-03 Assembly Manuel
2017-10-05 Add files via upload
    Wiring Diagram
